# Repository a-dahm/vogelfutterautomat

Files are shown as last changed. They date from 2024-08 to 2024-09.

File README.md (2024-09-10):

<p align="center">
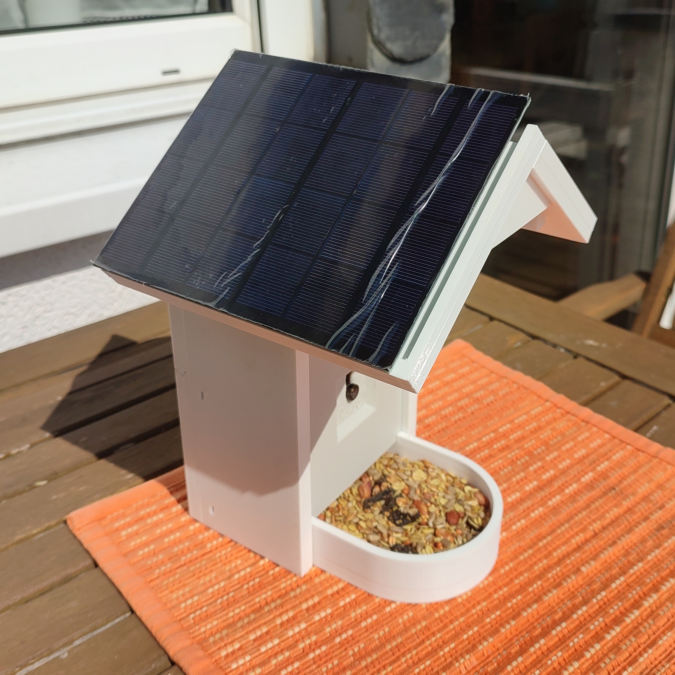
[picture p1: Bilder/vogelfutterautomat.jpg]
    
</p>

`⚠️ Dieses Projekt befindet sich zurzeit noch in der Prototyp-Phase. Der Prototyp ist funktionstüchtig, jedoch gibt es noch viel zu verbessern, damit das Gerät tatsächlich einen einsetzbaren Zustand erreicht. ⚠️`

<!-- omit in toc -->
# Inhaltsverzeichnis

- [Vogelfutterautomat](#vogelfutterautomat)
  - [Funktionsweise](#funktionsweise)
  - [Repository-Übersicht](#repository-übersicht)
  - [Materialübersicht](#materialübersicht)
  - [Anleitung](#anleitung)
    - [Firmware](#firmware)
      - [Arduino Pro Mini 3V](#arduino-pro-mini-3v)
      - [Seeed Studio XIAO ESP32S3 Sense](#seeed-studio-xiao-esp32s3-sense)
    - [Server](#server)
    - [Elektronik](#elektronik)
    - [Gehäuse](#gehäuse)
      - [Merkmale](#merkmale)
      - [Zusammenbau](#zusammenbau)

# Vogelfutterautomat

Bei diesem Projekt handelt es sich um einen Vogelfutterautomat mit integrierter Kamera und Mikrofon zur automatischen Durchführung von Bild- und Audioaufnahmen von Vögeln. Das Gerät kann die gesammelten Daten per WLAN an ein externes System übertragen oder diese auf einer SD-Karte speichern.

## Funktionsweise

Das Gerät basiert auf der Kombination eines Arduino Pro Mini und einem Seeed Studio XIAO ESP32S3 Sense. Als Stromversorgung dient ein Li-Po-Akku in Kombination mit einer Solarzelle und dem Solar Power Manager Board von DFRobot.

Der ESP32S3 führt mithilfe eines OV2640 Kamera-Moduls und dem integrierten Mikrofon Aufnahmen durch. Um den Stromverbrauch zu verringern wird die Stromversorgung des ESP32S3 durch den Arduino Pro Mini gesteuert. Der Arduino Pro Mini befindet sich dabei die meiste Zeit im Stromsparenden Deep-Sleep-Modus und wird mithilfe eines DS3231 Real-Time-Clock-Moduls sowie einem M5Stack AS312 PIR Bewegungssensor aufgeweckt.

Die Elektronik ist also wie folgt aufgebaut:

<p align="center">
    
</p>

Je nach Firmware-Konfiguration werden bei jeder Aufweckung Foto- und Audio-Aufnahmen durch den ESP32S3 erhoben. Die Daten können dann entweder auf einer SD-Karte gespeichert oder per WLAN an einen dafür eingerichteten Webserver übertragen werden.

## Repository-Übersicht

* Arduino: Firmware für den Arduino Pro Mini 3V
* ESP: Firmware für den Seeed Studio XIAO ESP32S3 Sense
* Elektronik: Zeichnung des Schaltkreises.
* Bilder: Enthält die in diesem Dokument verwendeten Bilder
* Gehäuse: STL- und Sketchup-Dateien für den 3D-Druck des Gehäuses
* Server: Software für den PHP-Server

## Materialübersicht

Das gesamte für den Zusammenbau benötigte Material (mit beispielhaften Links wo angebracht):

* Arduino Pro Mini 3V ([Berrybase](https://www.berrybase.de/arduino-pro-mini-328-3.3v/8mhz))
* Seeed Studio XIAO ESP32S3 Sense ([Berrybase](https://www.berrybase.de/seeed-xiao-esp32s3-sense-esp32-s3r8-wlan-ble-5.0-ov2640-kamerasensor-8mb-psram-8mb-flash))
* DS3231 Real-Time-Clock-Modul ([Eckstein-Shop](https://eckstein-shop.de/DS3231RTCModulI2CAT24C32forArduino2CwithLIR2032BatteryEN))
* PIR Modul ([Robotshop](https://eu.robotshop.com/de/products/m5stack-pir-bewegungssensor-as312))
* DFRobot Solar Power Manager ([Eckstein-Shop](https://eckstein-shop.de/DFRobotSolarPowerManager5VEN))
* Li-Po Akku
* Solarzelle
* OV2640 mit langem Ribbon-Cable und Weitwinkellinse ([Amazon](https://amazon.de/dp/B0BXSL76L8))
* 6x M3-Schraube sowie Mutter für die Fixierung des Gehäuses
* 4x M2-Schraube sowie Mutter für die Befestigung der Platine im Gehäuse
* Lochraster-Platine (70 x 50 mm) ([Eckstein-Shop](https://eckstein-shop.de/Lochrasterplatine50x70mmExperimentierplatineLC3B6tplatinePrototypeLeiterplattePCB2StC3BCcke))
* Lötmaterial (Platine, Verbindungskabel, Stiftleisten)

## Anleitung

### Firmware

Für das Anpassen und Überspielen der Firmware auf die beiden Mikroprozessor-Boards wird die [Arduino IDE](https://www.arduino.cc/en/software) benötigt. Als Einführung hier die offizielle (englische) Anleitung: [Link](https://docs.arduino.cc/software/ide-v2/tutorials/getting-started-ide-v2/)

Es werden für die Kompilierung die folgenden Bibliotheken benötigt, die zuvor über die Arduino IDE installiert werden müssen:

* [Low-Power (Rocket Scream Electronics)](https://www.arduino.cc/reference/en/libraries/low-power/): Verwaltung des Deep-Sleep-Modus für den Arduino Pro Mini 3V
* [RTCLib (Adafruit)](https://www.arduino.cc/reference/en/libraries/rtclib/): Kommunikation mit dem DS3231 Real-Time-Clock-Modul via I2C auf dem ESP32S3
* [NTPClient (Fabrice Weinberg)](https://www.arduino.cc/reference/en/libraries/ntpclient/): Für die Ermittlung der Uhrzeit via WLAN für das DS3231 Real-Time-Clock-Modul

#### Arduino Pro Mini 3V

Die Firmware für den Arduino Pro Mini befindet sich unter `Arduino/Arduino.ino`. Es sind hier keine Anpassungen am Quellcode notwendig.

Es ist jedoch wichtig zu beachten, dass vor dem Überspielen in der Arduino IDE unter "Werkzeuge" > "Processor" der Wert "ATmega328P (3,3V, 8 MHz)" ausgewählt wird (anstelle der 5V Variante):

<p align="center">
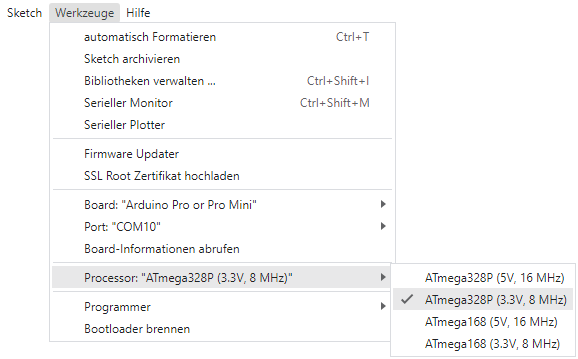
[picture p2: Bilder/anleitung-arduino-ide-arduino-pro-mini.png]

</p>

#### Seeed Studio XIAO ESP32S3 Sense

Die Firmware für den Seeed Studio XIAO ESP32S3 Sense befindet sich unter `ESP/ESP.ino`. Im Quellcode können die folgenden Einstellungen vorgenommen werden:

| Einstellung | Beschreibung | Beispiel |
| --- | --- | --- |
| `SERIAL_DEBUG` | Kann für Debug-Zwecke definiert werden, um Informationen über die UART-Schnittstelle des ESP32S3 ausgeben zu lassen | `//#define SERIAL_DEBUG` (deaktiviert) |
| `DATEN_MODUS` | Bestimmt, wie die mit den gesammelten Daten umgegangen wird. `DIREKT_UPLOAD`: Daten werden sofort bei Aufnahme hochgeladen und nicht zwischengespeichert. In diesem Modus wird keine SD-Karte benötigt. `TAEGLICHER_UPLOAD`: Aufnahmen werden auf der SD-Karte zwischengespeichert und am nächsten Morgen hochgeladen. `LOKAL`: Aufnahmen werden nur auf der SD-Karte gespeichert; die WLAN-Funktion wird hierbei dennoch eventuell für die Ermittlung der Uhrzeit verwendet, falls das RTC-Modul ausfällt. | `#define DATEN_MODUS DIREKT_UPLOAD` |
| `WARTE_VOR_FOTO` | Gibt eine Zeit (in Sekunden) an, die zwischen hochfahren und Foto gewartet werden soll. Dies dient dazu, dass sich der Kamera-Sensor an die Helligkeit der Umgebung anpassen kann, um unter-/überbelichteten Fotos vorzubeugen. | `#define WARTE_VOR_FOTO 2` |
| `AUDIOAUFNAHME_KURZ_DAUER` | Bestimmt die Länge der Audioaufnahme (in Sekunden) bei Aufweckung durch den Bewegungssensor. Maximalwert: 240 Sekunden. | `#define AUDIOAUFNAHME_KURZ_DAUER 5` |
| `AUDIOAUFNAHME_LANG_DAUER` | Bestimmt die Länge der Audioaufnahme (in Sekunden) bei Aufweckung durch das Real-Time-Clock-Modul. Dies dient dazu, den Vogelgesang am Morgen festzuhalten. Maximalwert: 240 Sekunden. | `#define AUDIOAUFNAHME_LANG_DAUER 60` |
| `WIFI_SSID` | Der Name des WLAN-Netzwerkes. | `#define WIFI_SSID "MeinWLAN"` |
| `WIFI_PASSWORD` | Das Passwort des WLAN-Netzwerkes. | `#define WIFI_PASSWORD "MeinPasswort"` |
| `UPLOAD_SERVER` | Die IP-Adresse des Webservers. | `#define UPLOAD_SERVER "192.168.178.50"` |
| `UPLOAD_PORT` | Der vom Webserver verwendete Port. Normalerweise ist dies bei HTTP der Port 80. | `#define UPLOAD_PORT 80` |
| `UPLOAD_PATH` | Der Pfad zum `upload.php`-Skript auf dem Webserver. Bei Ablage im Root-Verzeichnis lautet dieser `/upload.php` | `#define UPLOAD_PATH "/upload.php"` |

Vor dem Überspielen der Firmware muss unter "Werkzeuge" > "PSRAM" der Wert "OPI PSRAM" ausgewählt werden:

<p align="center">
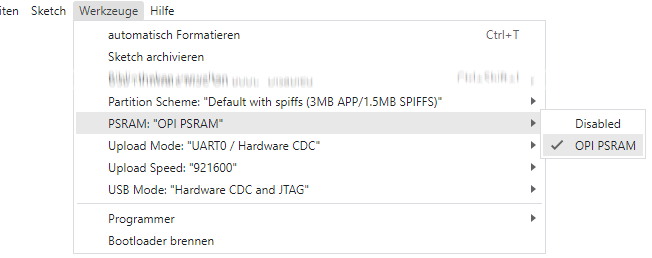
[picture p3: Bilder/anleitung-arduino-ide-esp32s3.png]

</p>

### Server

Die Server-Seite verwendet HTML & PHP. Dafür muss eine entsprechende Server-Software auf einem geeigneten Gerät installiert werden. Das verwendete Gerät sollte soweit möglich durchgehend erreichbar sein, damit jederzeit Uploads stattfinden können. Es wird daher empfohlen, dafür zum Beispiel einen Raspberry Pi oder einen Mini-PC zu verwenden.

Um die Server-Seite zu hosten wird Apache & PHP verwendet. Die Installation dieser Komponenten hängt vom Betriebssystem ab:

* Unter Windows kann [XAMPP](https://www.apachefriends.org/de/index.html) verwendet werden.
* Für eine Anleitung zur Installation von Apache & PHP unter Linux sollte je nach Distribution nach einer Anleitung gesucht werden. Beispielsweise hier die [Installation unter Ubuntu](https://wiki.ubuntuusers.de/PHP/#Installation-fuer-serverseitige-Programmierung).

Nach der Installation können die Dateien aus dem "Server"-Verzeichnis dieses Repositories im entsprechenden Root-Verzeichnis des Webservers abgelegt werden: unter Windows der Ordner `Apache\htdocs`, unter Linux standardmäßig `/var/www/html`. Falls die Dateien in einem Unterverzeichnis abgelegt werden (zum Beispiel weil bereits andere Webseiten gehostet werden) muss der entsprechende Pfad in der `ESP.ino` eingetragen werden.

In dem Verzeichnis befinden sich auch zwei Log-Dateien `log.txt` und `errors.txt`. In diese Textdateien werden nach jedem erfolgten Upload rudimentäre Informationen festgehalten um potentielle Probleme zu diagnostizieren.

Damit die Webseite durch den ESP32S3 gefunden werden kann muss die IP-Adresse in der `ESP.ino` eingetragen werden (unter `#define UPLOAD_SERVER`).

* Anleitung für Windows [hier](https://support.microsoft.com/de-de/windows/suchen-sie-ihre-ip-adresse-in-windows-f21a9bbc-c582-55cd-35e0-73431160a1b9)
* Anleitung für Linux [hier](https://www.ionos.de/digitalguide/hosting/hosting-technik/linux-ip-adresse-anzeigen/)

### Elektronik

Der Schaltplan der Platine ist im Verzeichnis `Elektronik` zu finden. Die `.fzz`-Datei kann mit der Software [Fritzing](https://fritzing.org/) eingesehen werden. Bei Fritzing handelt es sich zwar um Open-Source Software, jedoch wird die kompilierte Version nur gegen Zahlung vertrieben. Falls die Software also nicht verwendet werden kann, finden Sie hier einen Screenshot des Schaltplans:

<p align="center">
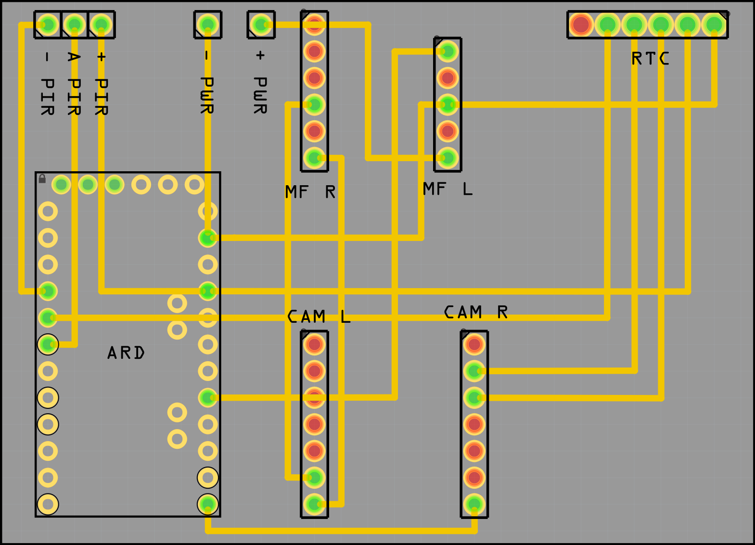
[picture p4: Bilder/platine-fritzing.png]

</p>

Dabei wurden für die Anschlüsse mit der Bezeichnung `-/A/+ PIR` (oben links) einfache Stiftleisten verwendet. Für `-/+ PWR` (oben links) wurden Schraubklemmen gewählt. Das RTC-Modul (rechts) wurde mit 90° gebogenen Stiften versehen und deshalb auch mit 90°-Winkel Stiftleisten auf der Platine befestigt.

Die fertiggestellte Platine inklusive der einzelnen Komponenten sieht Schlußendlich wie folgt aus:

<p align="center">
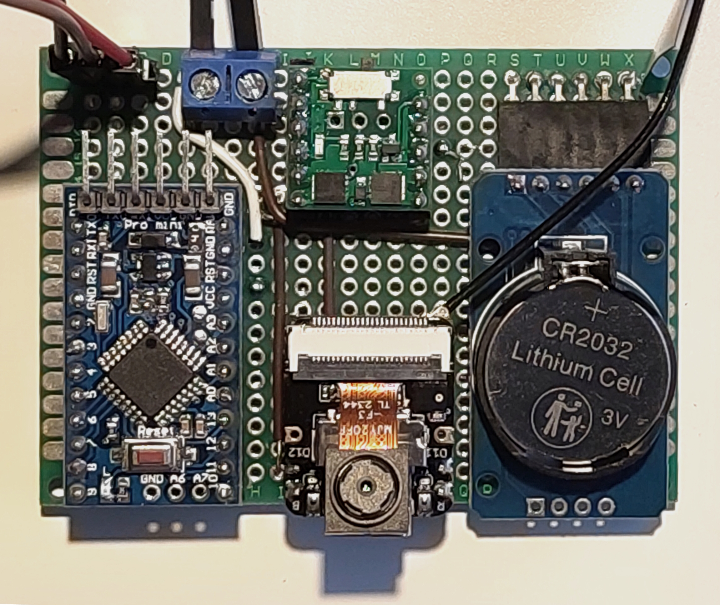
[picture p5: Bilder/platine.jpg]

</p>

### Gehäuse

Die Modell-Dateien für das Gehäuse können im Verzeichnis `Gehäuse` gefunden werden.

Das Gehäuse wurde für die Herstellung mittels 3D-Druck konzipiert. Neben den einzelnen Bauteilen im `STL`-Dateiformat wurde auch das komplette Modell als [Sketchup](https://www.sketchup.com/)-Datei (`SKP`-Dateiformat) hinterlegt. Dadurch können eigene Anpassungen durchgeführt werden, soweit dies erforderlich ist.

<p align="center">
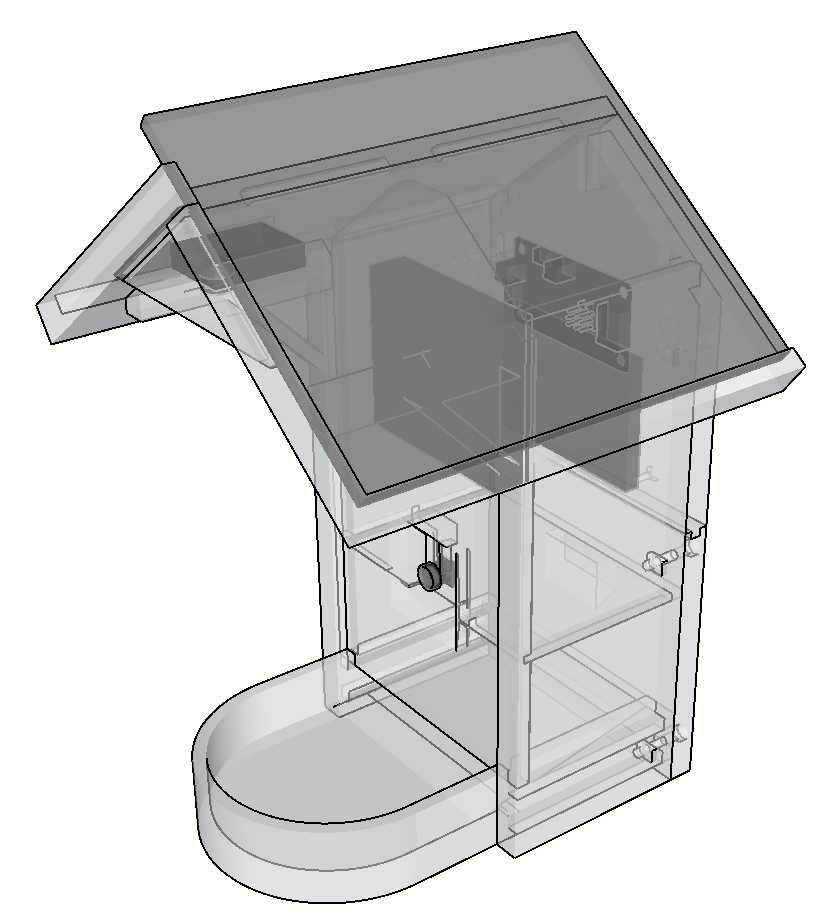
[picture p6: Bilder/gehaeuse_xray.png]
    
</p>

In der Sketchup-Datei wurden auch die restlichen Komponenten, wie beispielsweise die Solarzelle und das Kamera-Modul, eingezeichnet. Falls sich diese Maße von denen Ihrer Komponenten unterscheided, was beispielsweise bei der gelöteten Platine der Fall sein kann, müssen eventuell hier Anpassungen durchgeführt werden.

Falls kein eigener 3D-Drucker zur Verfügung steht kann die Produktion des Gehäuses auch durch einen Dienstleister durchgeführt werden lassen. Dazu reicht es aus, die `STL`-Dateien an diesen zu übergeben.

Bei der eigenen Herstellung sollte darauf geachtet werden, ob es möglich ist, ein Hitzebeständigeres Material als PLA zu verwenden, da dieses eventuell unter intensiver Sonneneinstrahlung die Erweichungstemperatur erreicht. Empfohlen wird hier der Druck mittels PETG-Filament. Die Druckzeit unterscheided sich je nach Drucker, Filament und Konfiguration immens. Ein Testdruck, der auf einem Prusa I3 MK3S+ mit PETG-Filament durchgeführt wurde, dauerte insgesamt circa 45 Stunden.

Fast alle Bauteile des Gehäuses werden per Steckverbindung zusammengefügt. Dabei kann die Toleranz dieser Verbindungen jedoch nicht im Allgemeinen für jeden Drucker korrekt in den gebotenen Modell-Dateien geboten werden. Daher wird es sehr wahrscheinlich notwendig sein, die einzelnen Steckverbindungen mit Feile oder anderen Schleifmethoden nachzubearbeiten, bis die Steckverbindungen der Bauteile zusammenpassen.

#### Merkmale

Die Solarzelle kann beliebig links oder rechts auf dem Dach platziert werden. Das Verbindungskabel wird dann über die Rückseite durch eine Öffnung direkt unterhalb des Daches in die innere Kammer geführt:

<p align="center">
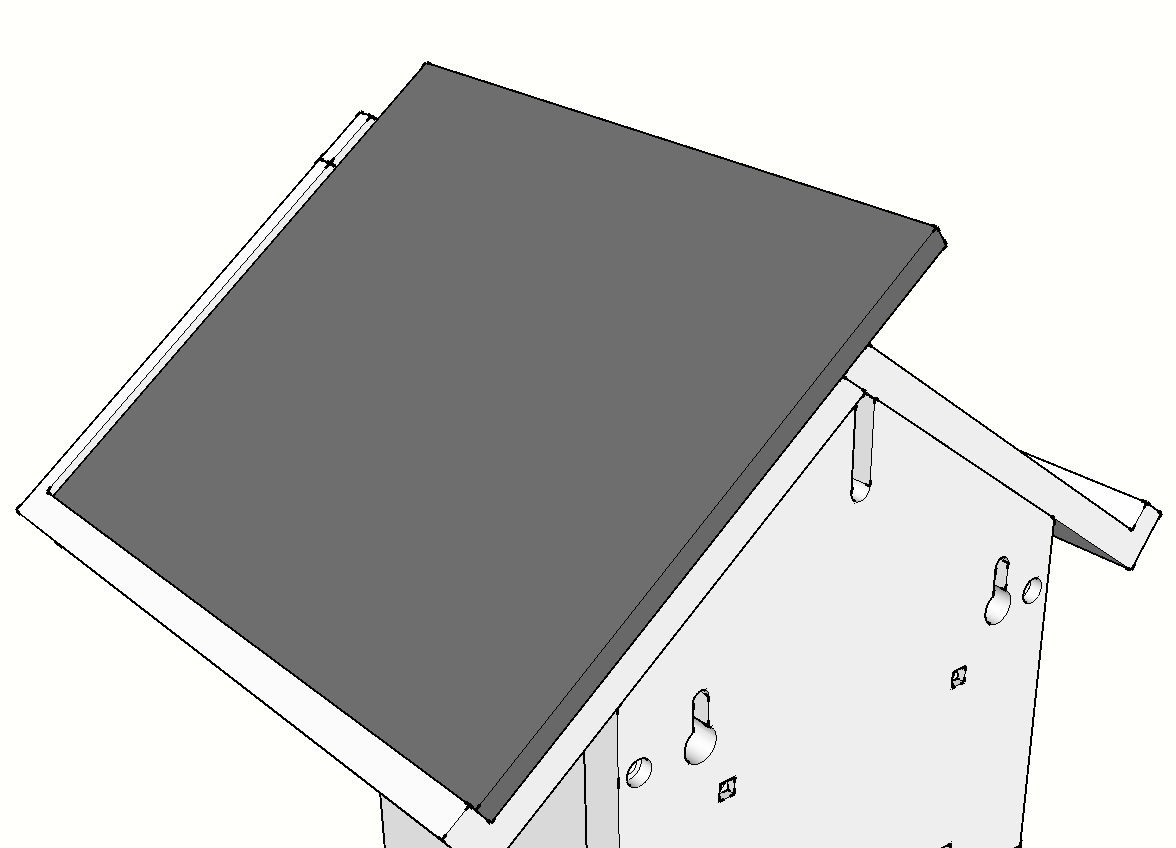
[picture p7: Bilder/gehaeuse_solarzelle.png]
    
</p>

Der PIR-Bewegungssensor wurde unter dem Dach platziert und nach unten auf den Futtertrog ausgerichtet. Die Kabel des Sensors werden unter dem Dach durch eine Öffnung ins Innere geführt:

<p align="center">
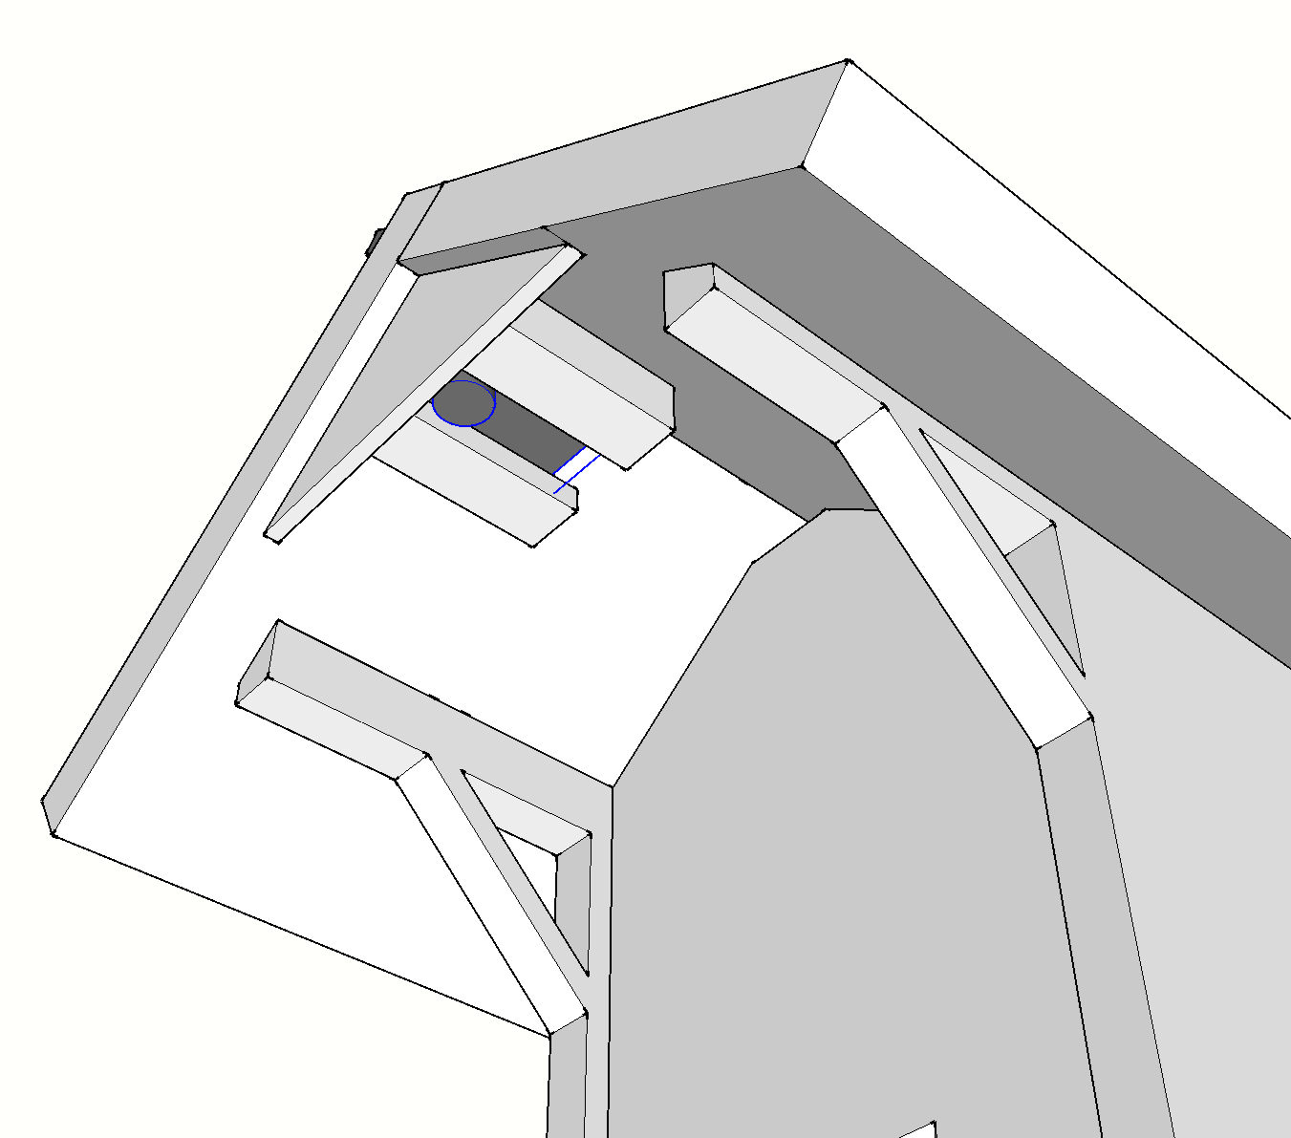
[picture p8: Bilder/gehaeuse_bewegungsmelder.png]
    
</p>

Die Linse des OV2640-Kamera-Moduls wird auf der Vorderseite des Gehäuse platziert. Diese wird von oben in einen Schlitz eingeführt, um die Linse zu fixieren:

<p align="center">
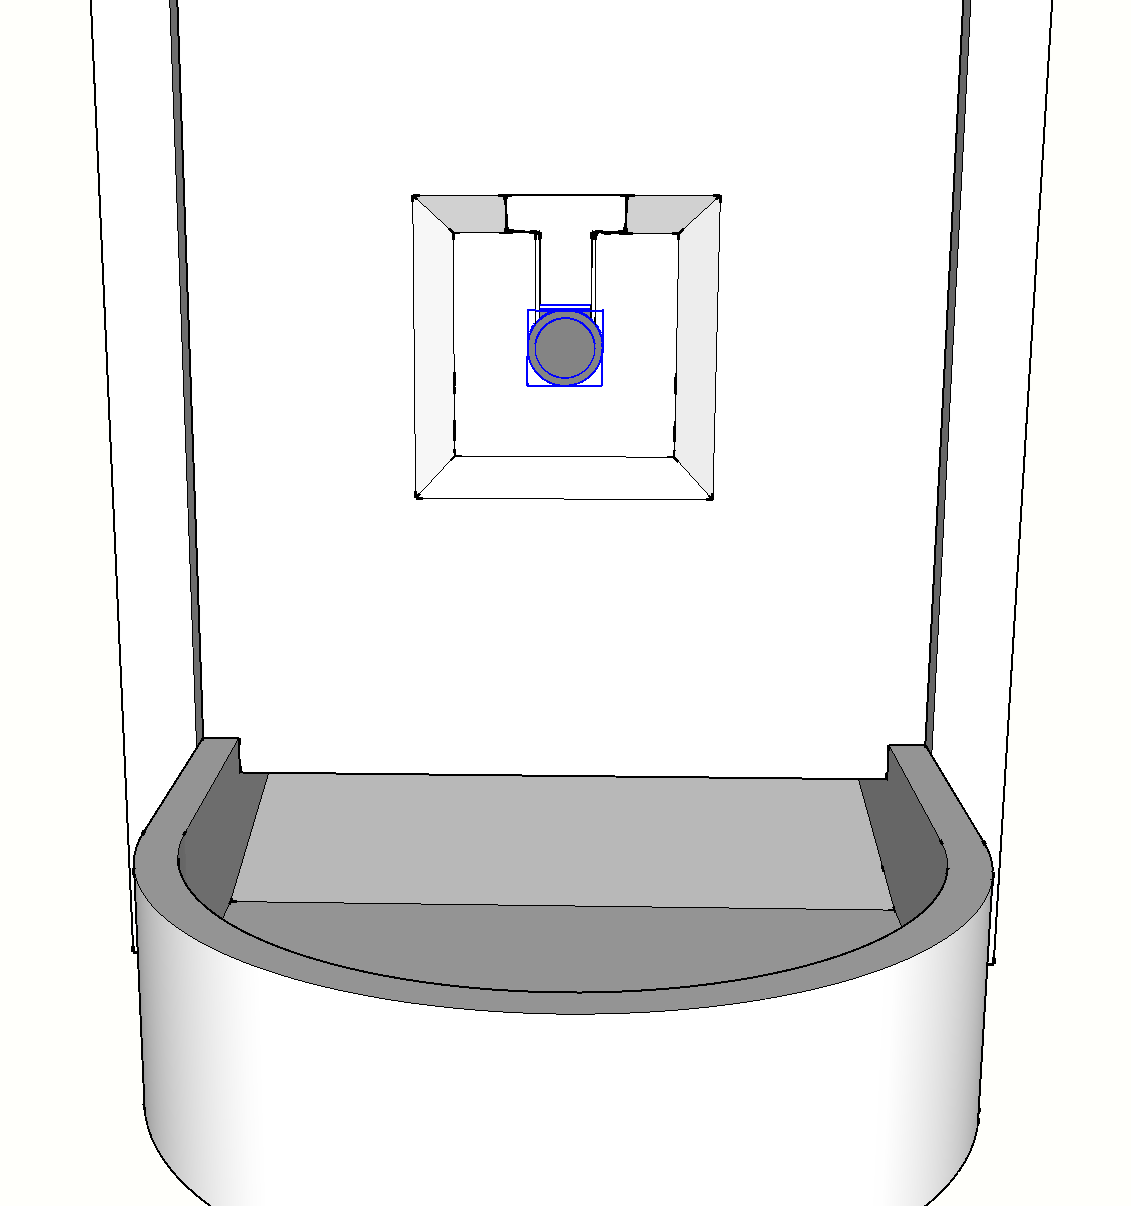
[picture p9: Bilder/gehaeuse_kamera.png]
    
</p>

Die restliche Elektronik wurde im inneren des Gehäuses platziert. Der Li-Po Akku (links) wird mit doppelseitigem Klebeband über der Kamera an der Vorderwand fixiert. Das DFRobot Solar Power Manager Board wird ohne fixierung im unteren Bereich abgelegt. Die Platine mit den restlichen Komponenten (rechts) wird gegenüber der Kamera mittels 4 M2 Schrauben und Muttern an der Rückwand befestigt.

<p align="center">
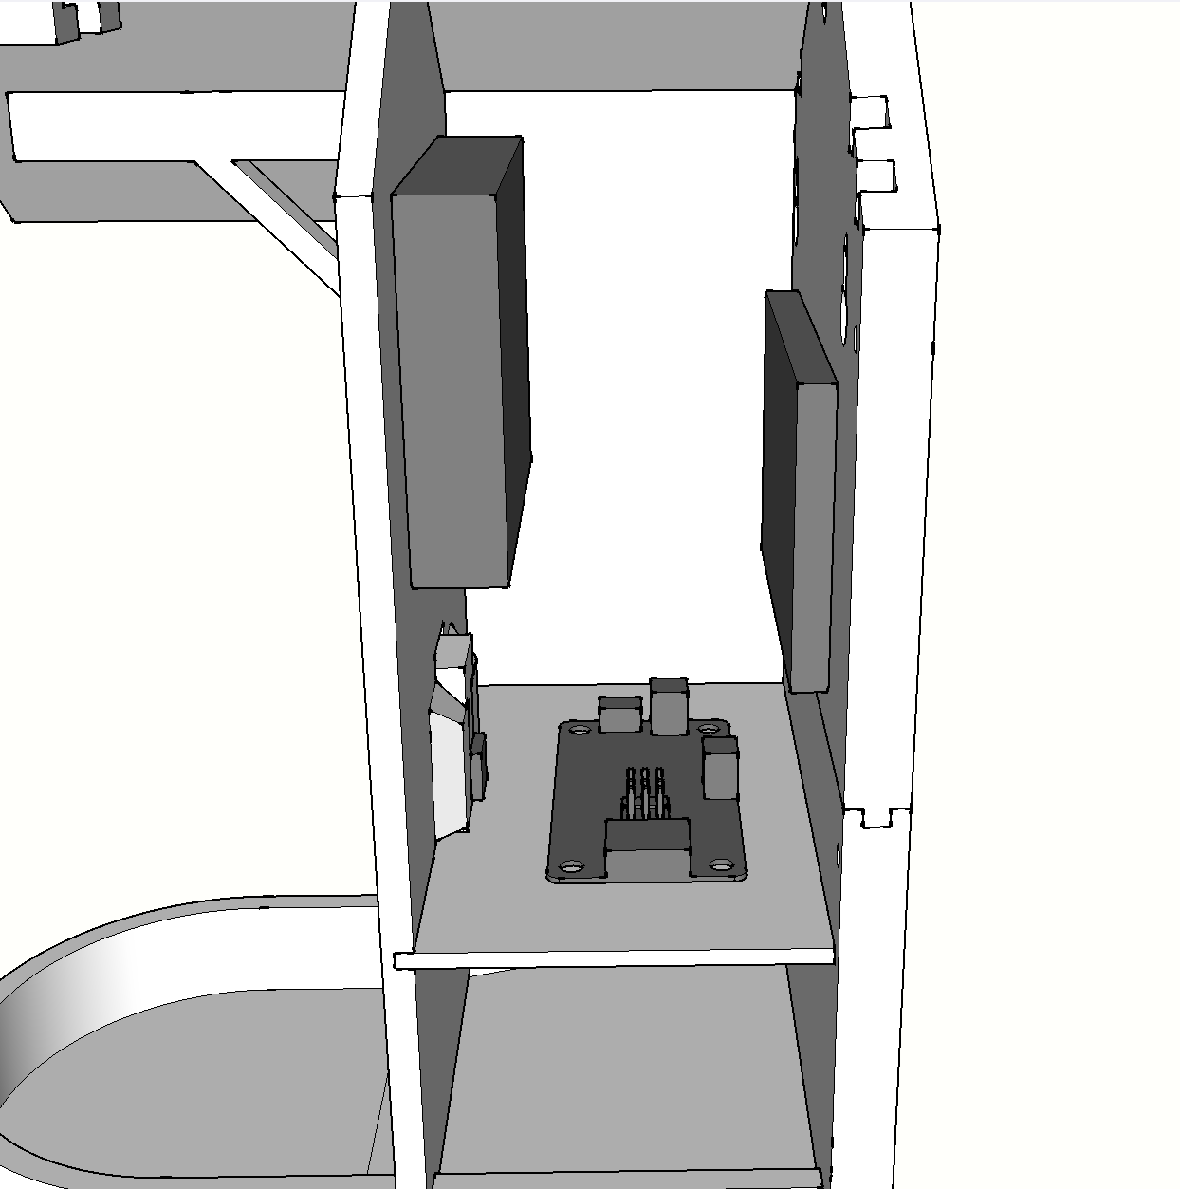
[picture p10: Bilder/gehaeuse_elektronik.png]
    
</p>

Auf der Rückseite des Gehäuse befindet sich eine Öffnung, um Vogelfutter nachzufüllen. Zudem befinden sich hier zwei Öffnungen, durch die der Vogelfutterautomat mittels Schrauben an einer Hauswand befestigt werden.

<p align="center">
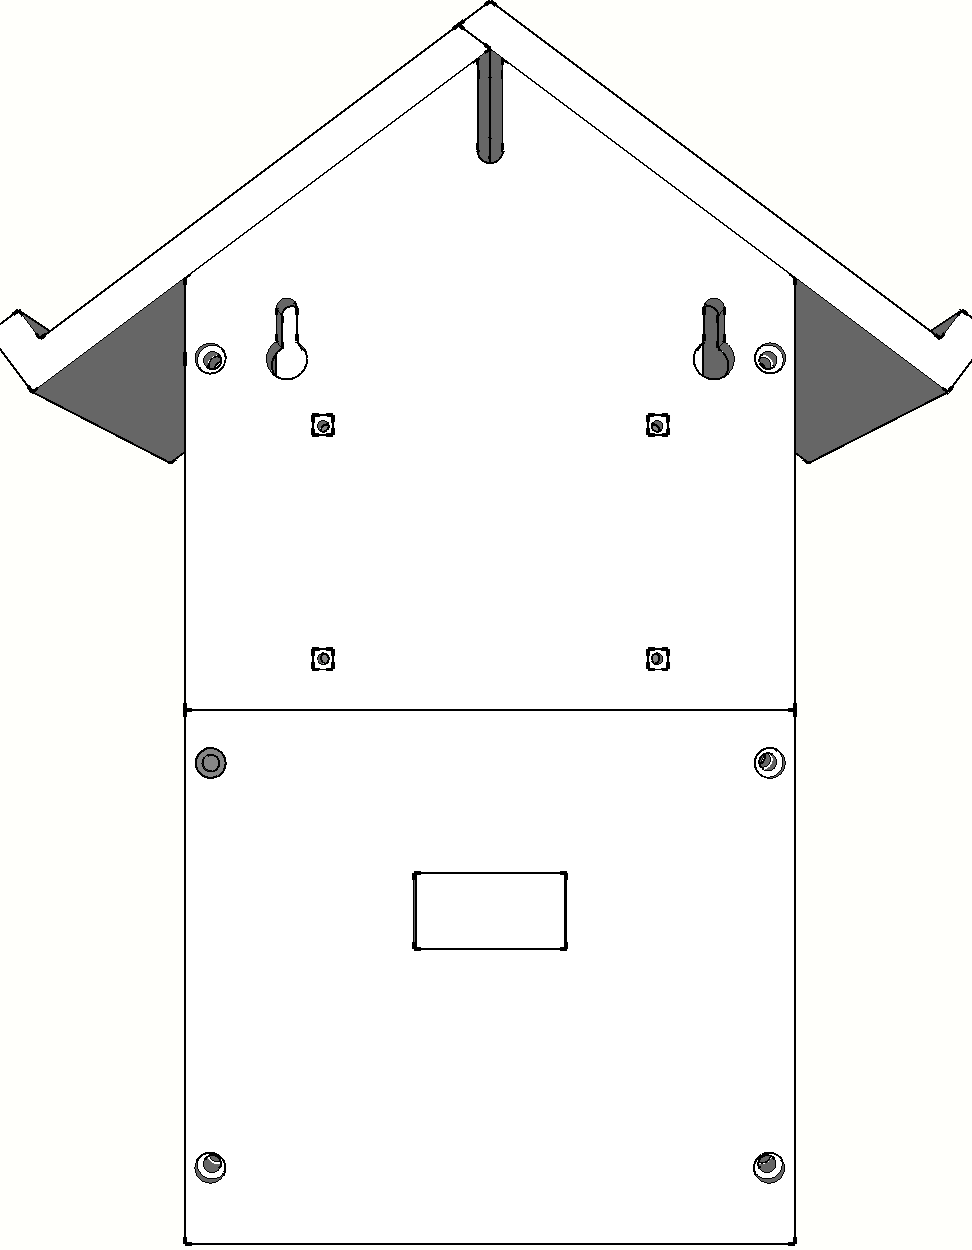
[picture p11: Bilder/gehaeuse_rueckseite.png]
    
</p>

#### Zusammenbau

Der Zusammenbau des Gehäuses ist weitestgehend selbsterklärend. Zunächst wird der Li-Po Akku mit doppelseitigem Klebeband an der Rückseite der Vorderwand befestigt. Dabei sollte darauf geachtet werden, dass das Kabel des Akkus nach unten ausgerichtet ist.

<p align="center">
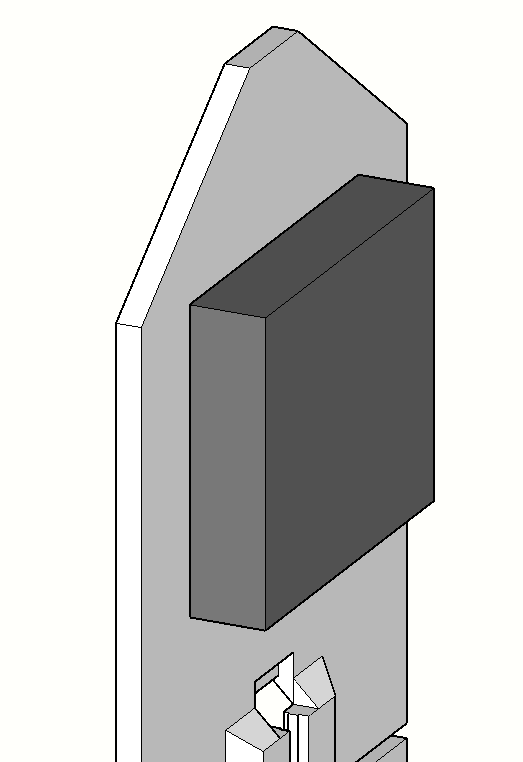
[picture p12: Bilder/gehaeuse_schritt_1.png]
    
</p>

Vom Futtertrog ausgehend werden die Vorderwand, der untere Teil der Rückwand und der Kammer-Separator zusammengesteckt:

<p align="center">
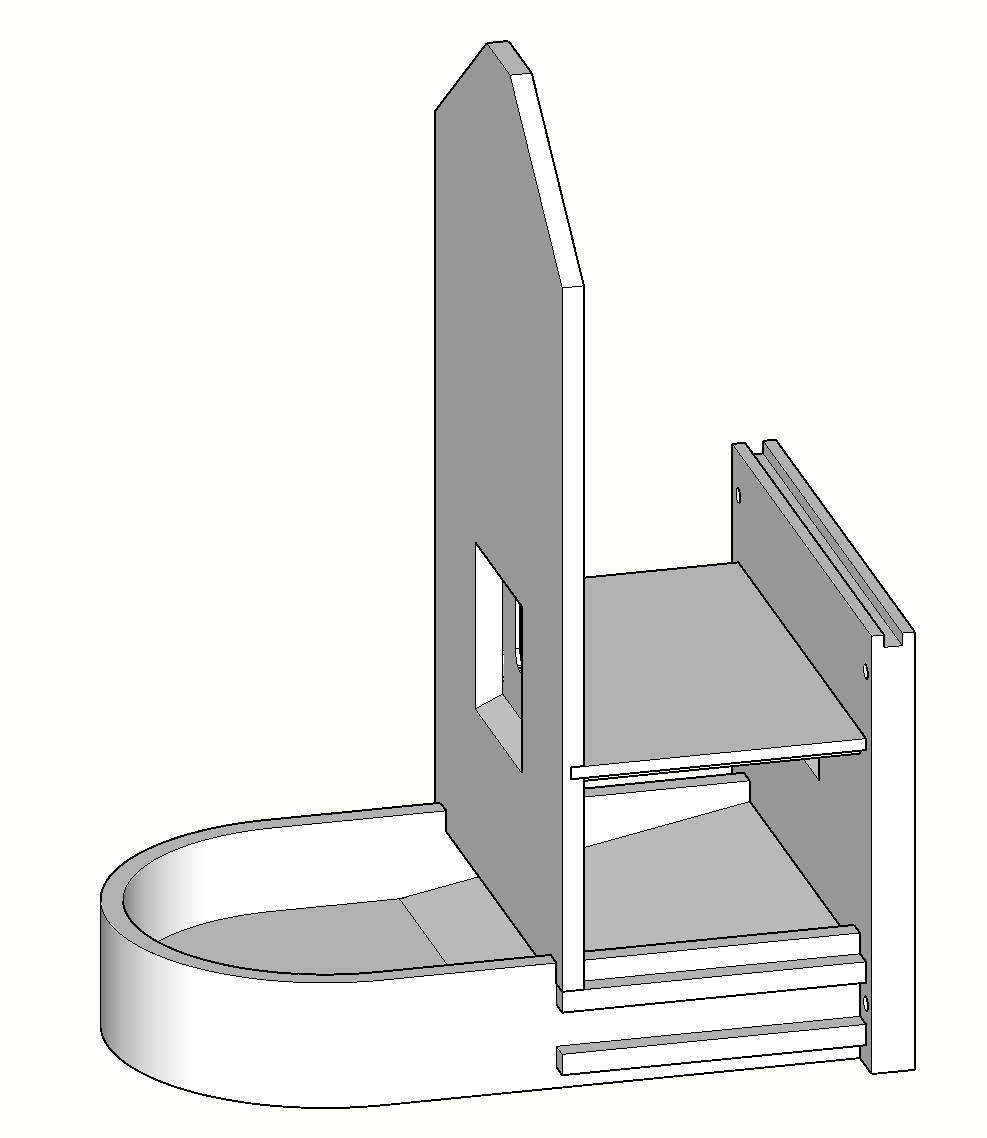
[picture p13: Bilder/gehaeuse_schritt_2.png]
    
</p>

Das Dach wird dann zunächst separat inklusive der PIR-Sensorhalterung zusammengesteckt:

<p align="center">
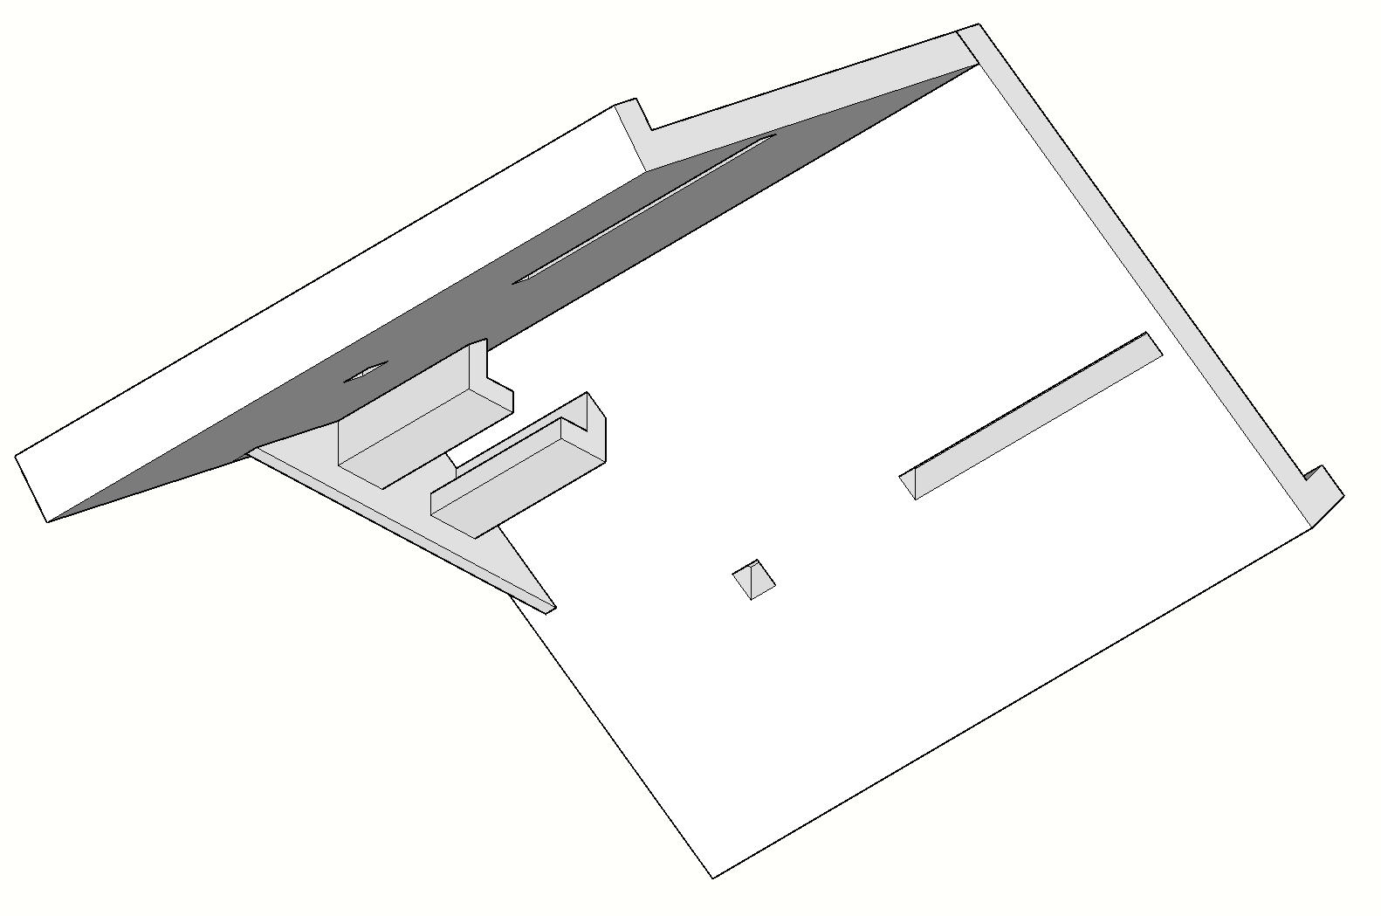
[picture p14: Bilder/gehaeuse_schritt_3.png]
    
</p>

Die Elektronik wird an der noch separierten oberen Rückwand mittels 4 M2 Schrauben und Muttern befestigt:

<p align="center">
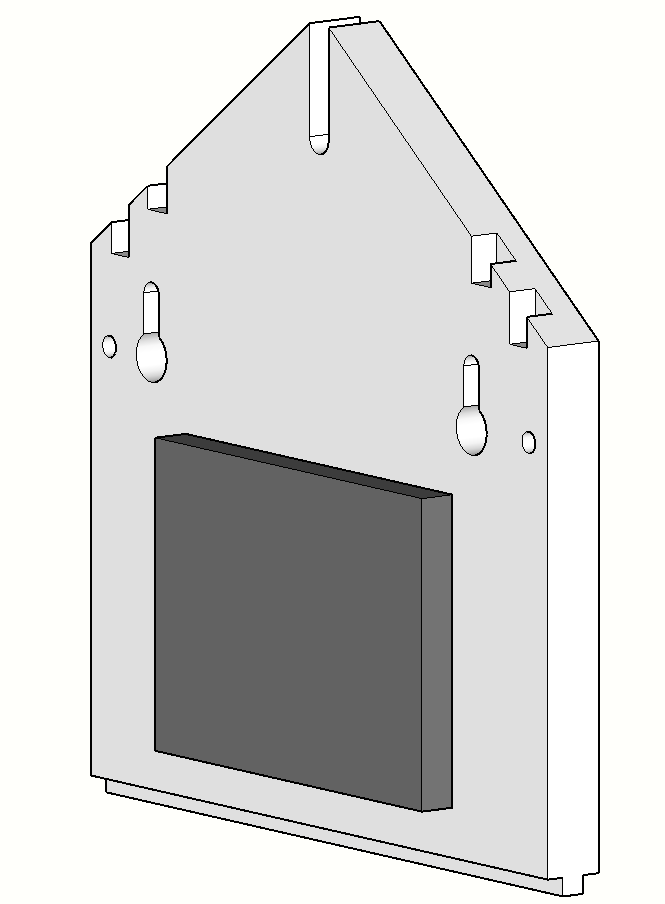
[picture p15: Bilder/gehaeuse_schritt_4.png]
    
</p>

Das Kamera-Modul wird dann von oben in die dafür vorgesehene Halterung in der Vorderwand eingeführt. Eventuell muss hierfür die Linse etwas verstellt werden:

<p align="center">
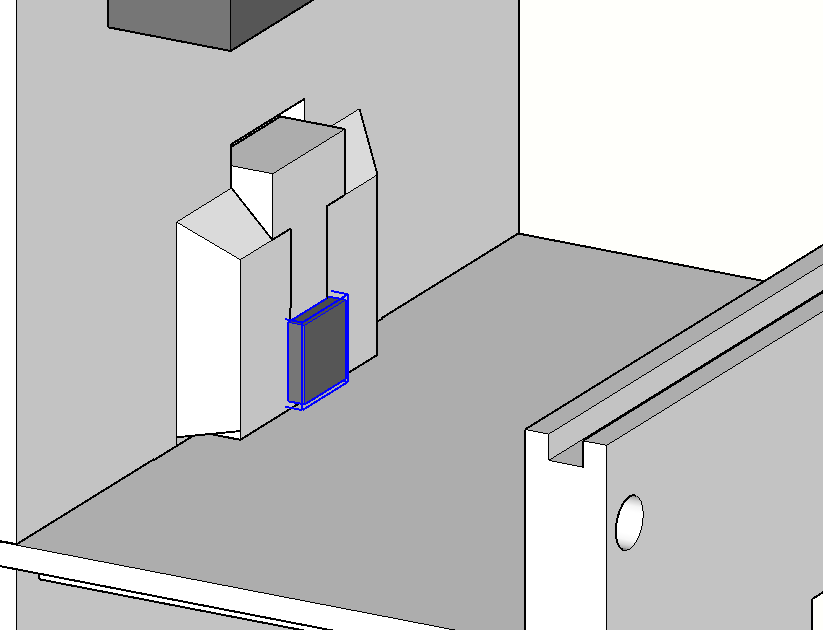
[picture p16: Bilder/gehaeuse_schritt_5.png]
    
</p>

Das Solar Power Manager Board wird dann im Inneren der Kammer platziert und zunächst nur mit dem Li-Po Akku verbunden:

<p align="center">
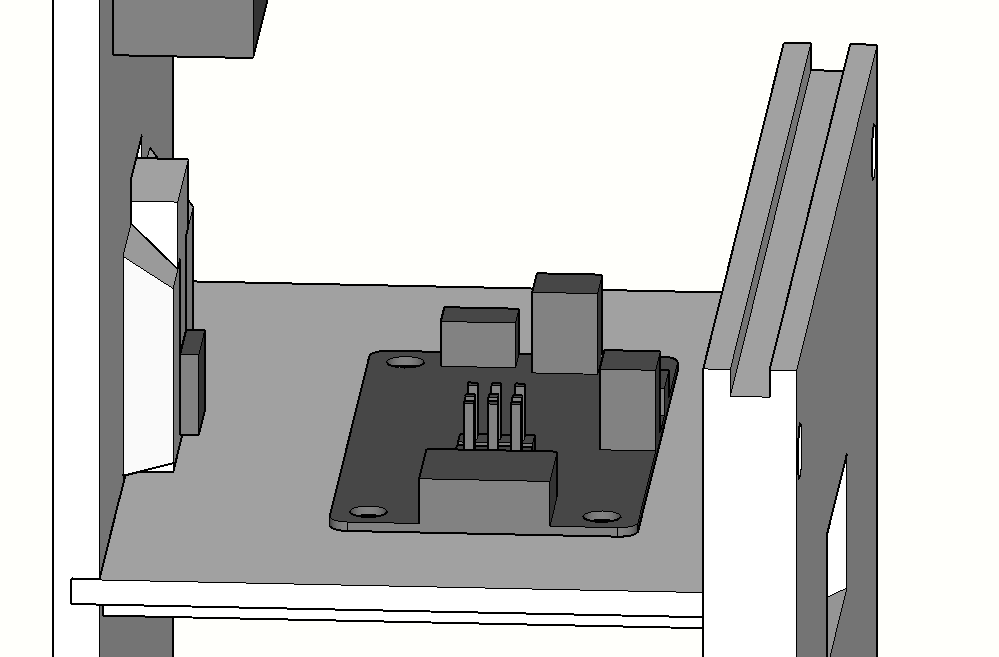
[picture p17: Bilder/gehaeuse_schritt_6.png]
    
</p>

Nun wird der obere Teil der Rückwand inklusive der Platine sowie eine der Seitenwände angesteckt. Die Seitenwand wird dann mit 3 M3 Schrauben und Muttern an den beiden Teilen der Rückwand fixiert. Dazu wird zunächst jeweils eine M3 Mutter in die dafür vorgesehenen rechteckigen Öffnungen auf den Seitenwänden gepresst, sodass diese nicht mehr rotieren kann. Dann kann durch die Rückwand hindurch jeweils eine M3 Schraube in jede Mutter eingeführt und fixiert werden:

<p align="center">
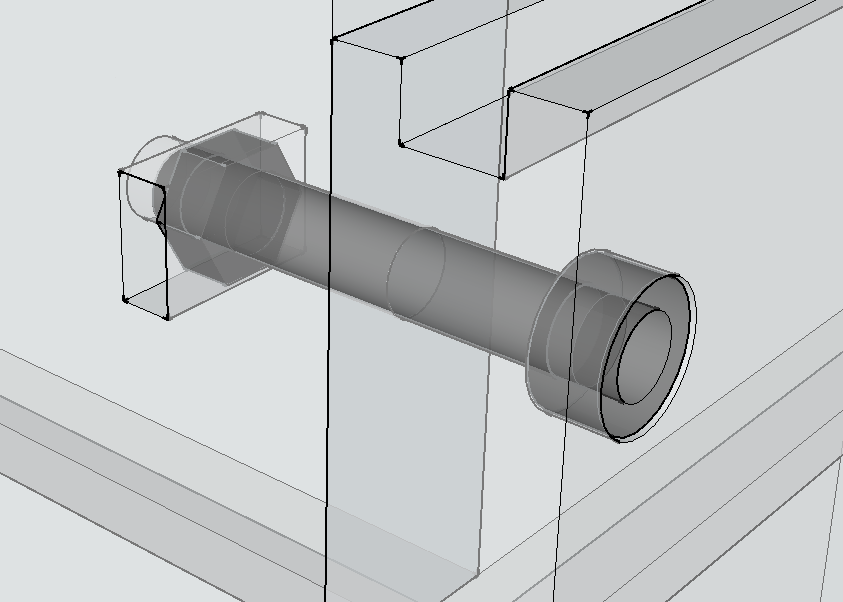
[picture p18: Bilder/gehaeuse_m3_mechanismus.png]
    
</p>

Nun kann die Stromversorgung des Solar Power Manager Boards mit der Platine verbunden werden. Zudem wird auch das Kamera-Modul an den XIAO ESP32S3 Sense angeschlossen.

<p align="center">
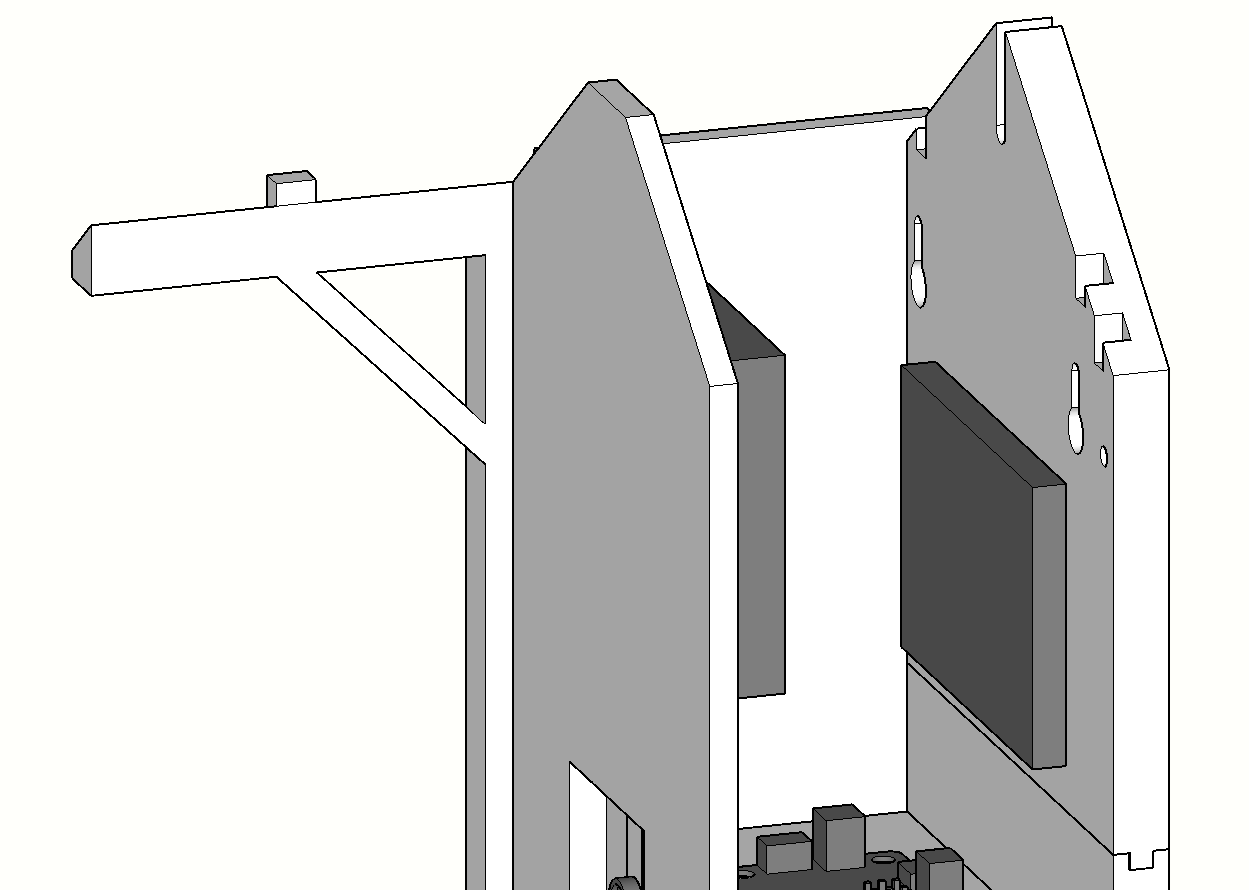
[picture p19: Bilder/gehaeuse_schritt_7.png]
    
</p>

Ohne das Dach bereits aufzustecken wird nun der Anschluss der Solarzelle durch die obere Öffnung der Rückwand geführt und an das Solar Power Manager Board angeschlossen. Zudem wird die Verkabelung des PIR-Bewegungsmelders mit der Platine durchgeführt. Falls dies in der Konfiguration der Firmware vorgesehen ist, wird in diesem Schritt auch die SD-Karte in den SD-Kartenleser des XIAO ESP32S3 Sense gesteckt. Jetzt kann die zweite Seitenwand angebracht werden. Diese wird ebenfalls durch 3 M3 Schrauben und Muttern an der Rückwand befestigt.

<p align="center">
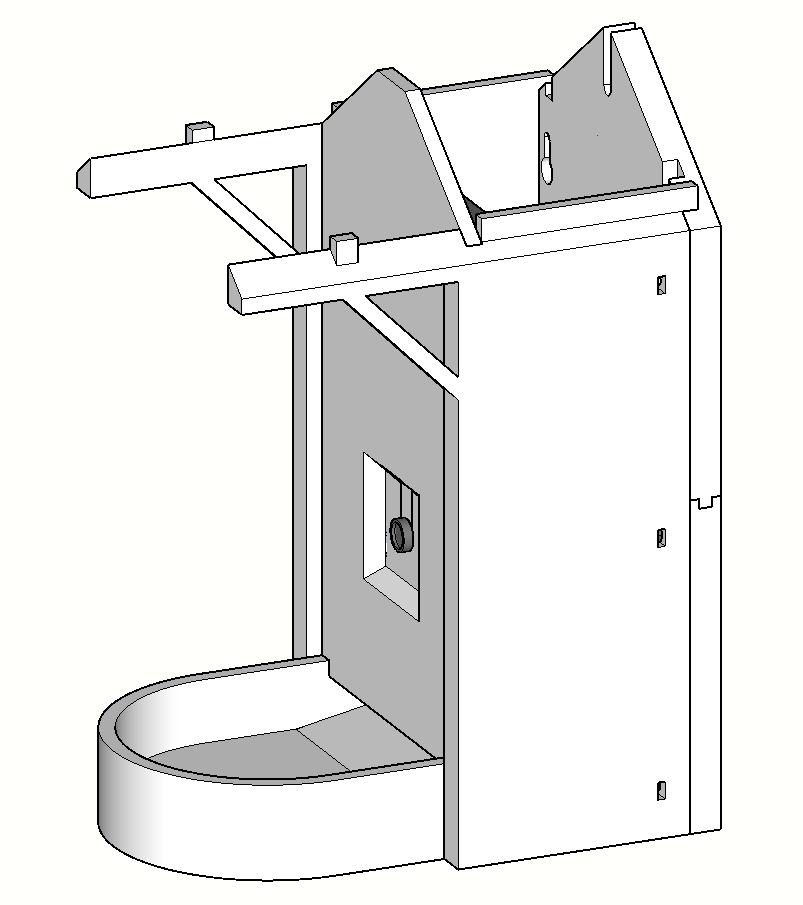
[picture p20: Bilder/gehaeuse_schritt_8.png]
    
</p>

Im letzten Schritt wird das Dach auf der Oberseite des Gerätes aufgesteckt. Hierbei muss darauf geachtet werden, dass die Kabel des PIR-Bewegungsmelder über die Flache Kante der Vorderwand von Außen in die innere Kammer geführt wurden, ohne dass diese durch das Dach gequetscht werden.

<p align="center">
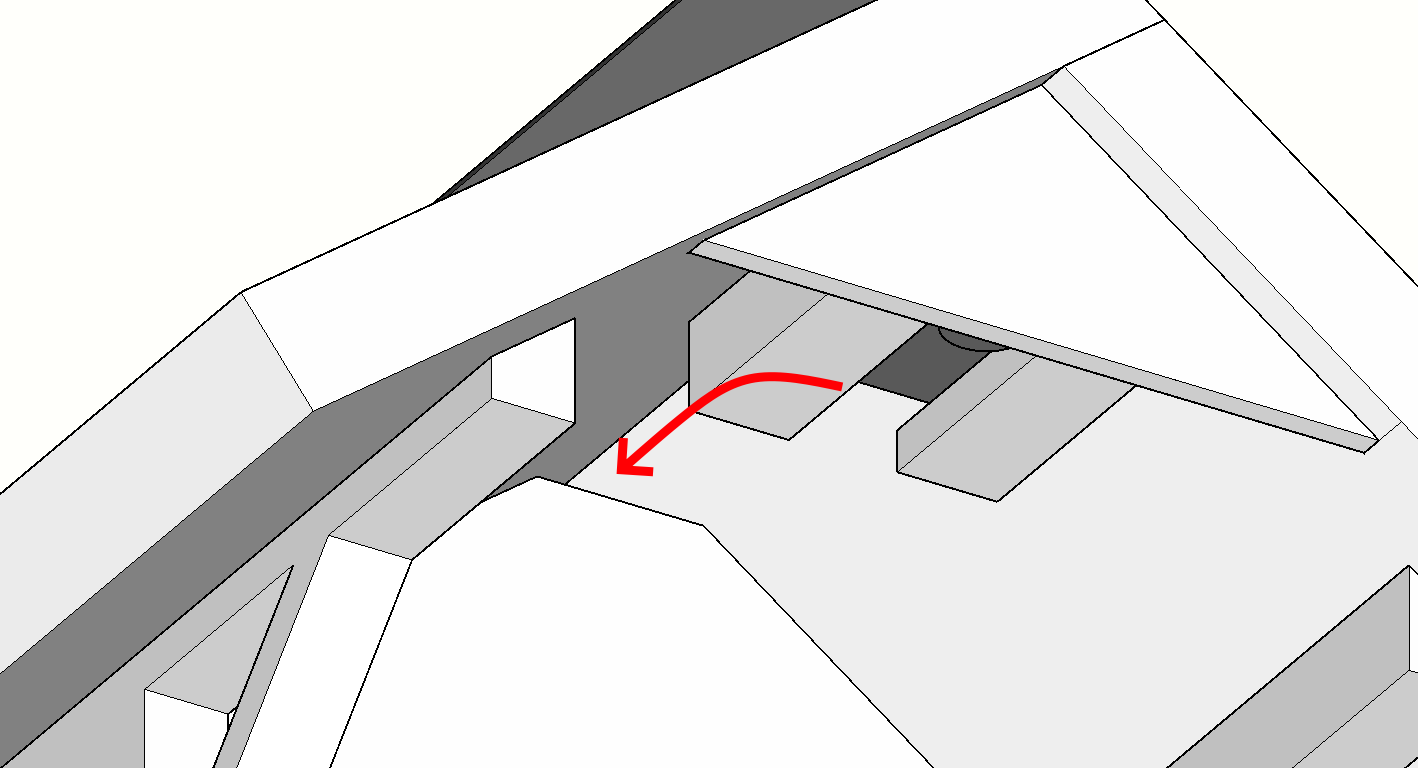
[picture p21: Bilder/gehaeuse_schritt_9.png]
    
</p>

Der PIR-Bewegungssensor wird dann in der dafür vorgesehenen Halterung an der Unterseite des Daches befestigt. Die Solarzelle wird auf der Seite des Daches platziert. Damit ist der Zusammenbau abgeschlossen.

<p align="center">
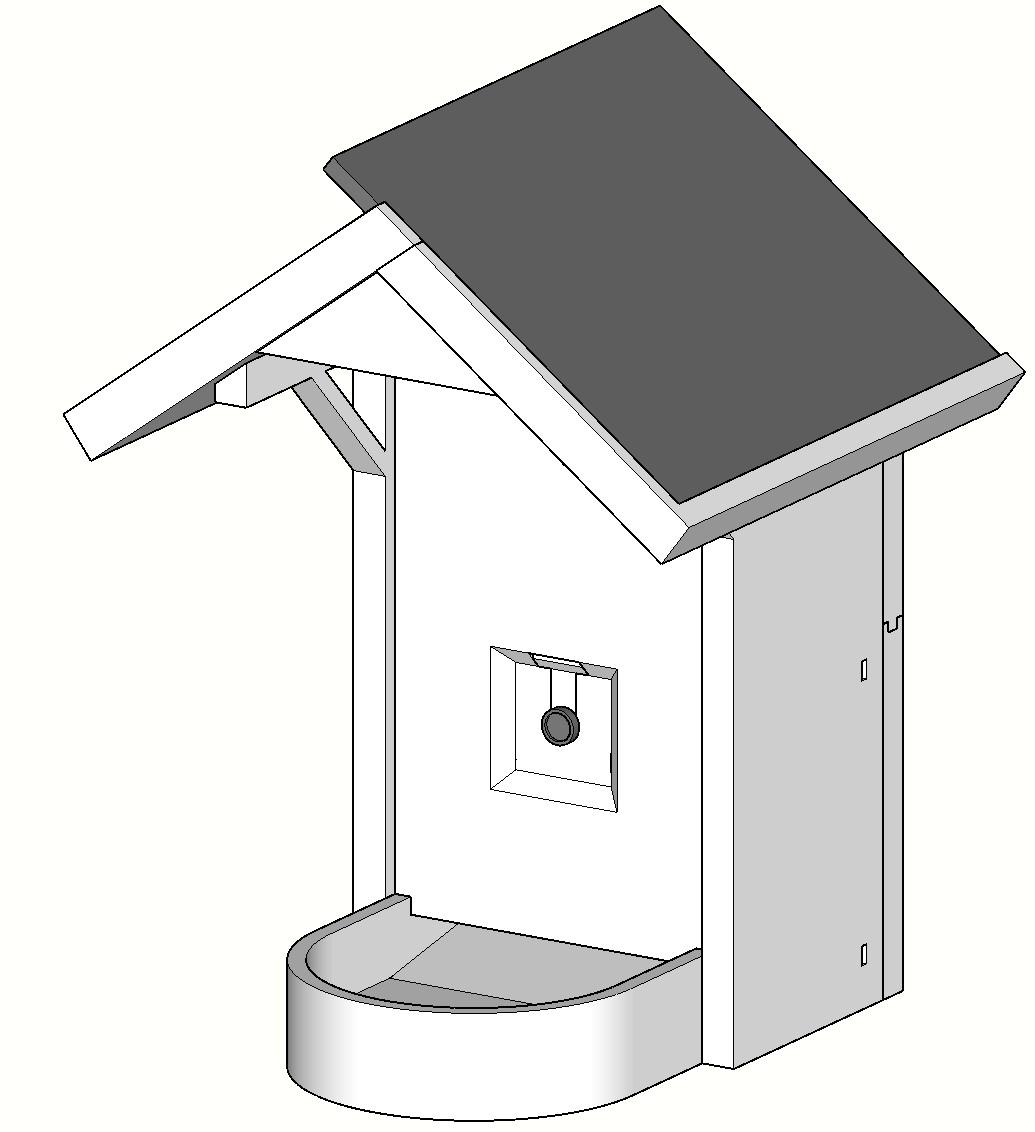
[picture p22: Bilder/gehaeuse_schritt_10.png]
    
</p>

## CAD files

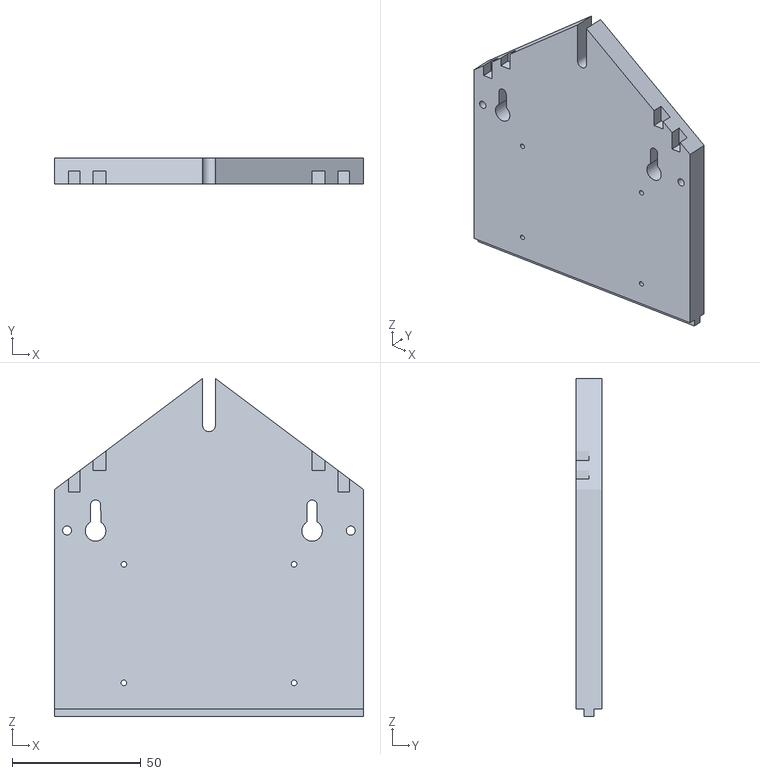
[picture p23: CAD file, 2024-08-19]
Gehäuse/Back_Wall_Top.stl
120.0 x 10.0 x 131.1

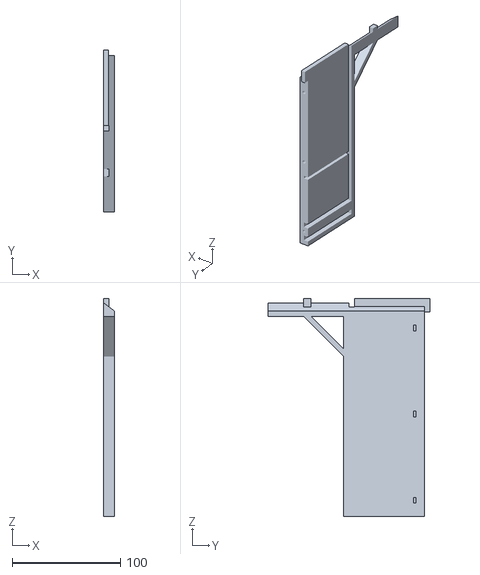
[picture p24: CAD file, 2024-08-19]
Gehäuse/Right_Wall.stl
10.0 x 150.0 x 201.5

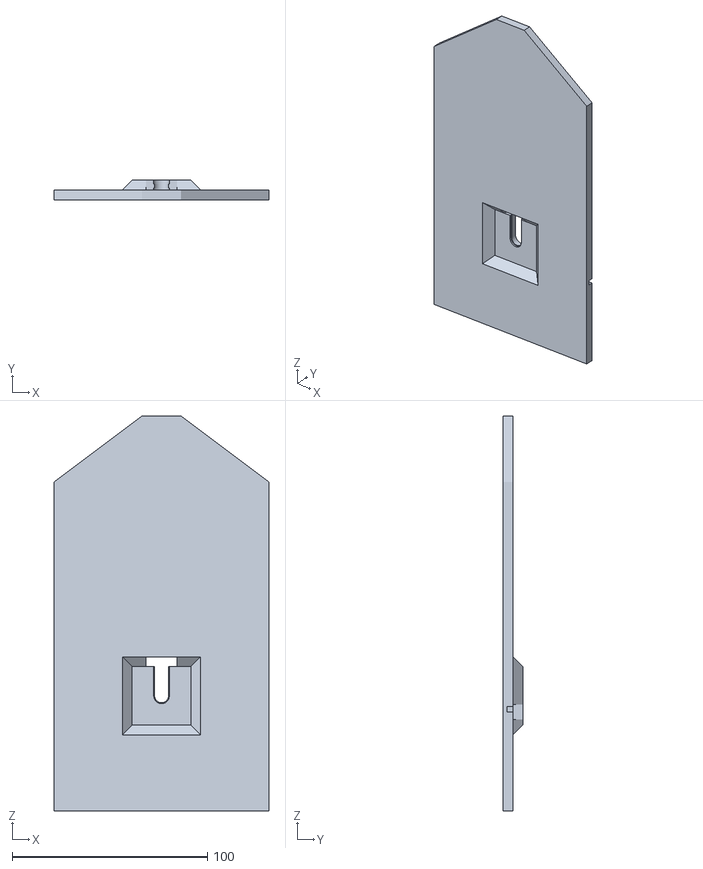
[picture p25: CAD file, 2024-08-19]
Gehäuse/Front_Wall.stl
110.0 x 10.0 x 202.5

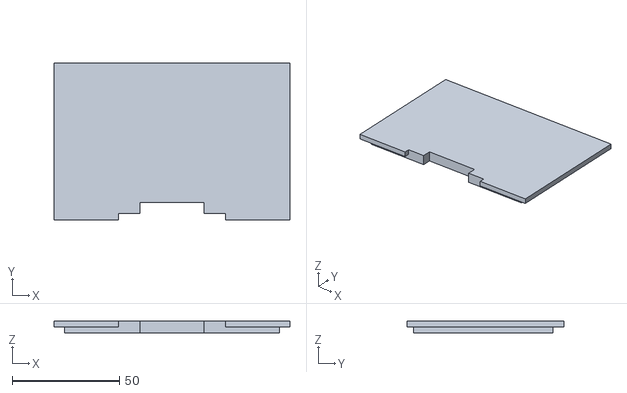
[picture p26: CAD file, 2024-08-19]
Gehäuse/Separator.stl
110.0 x 73.0 x 5.50

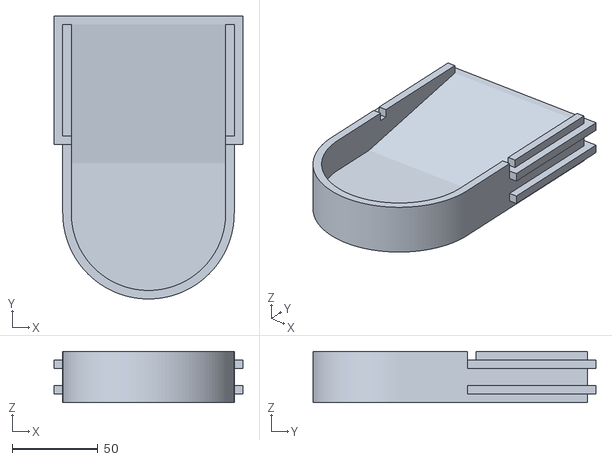
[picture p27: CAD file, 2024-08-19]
Gehäuse/Bottom_Tray.stl
110.0 x 165.0 x 30.0

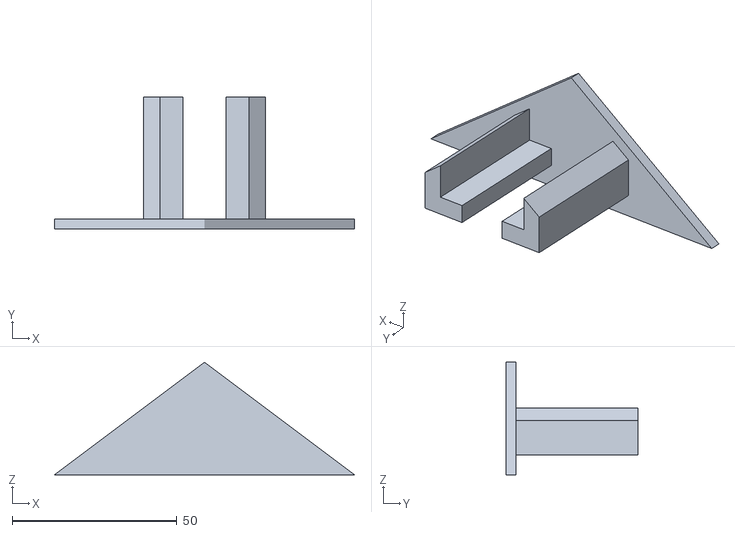
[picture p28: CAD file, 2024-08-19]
Gehäuse/PIR_Insert.stl
91.0 x 40.0 x 34.1

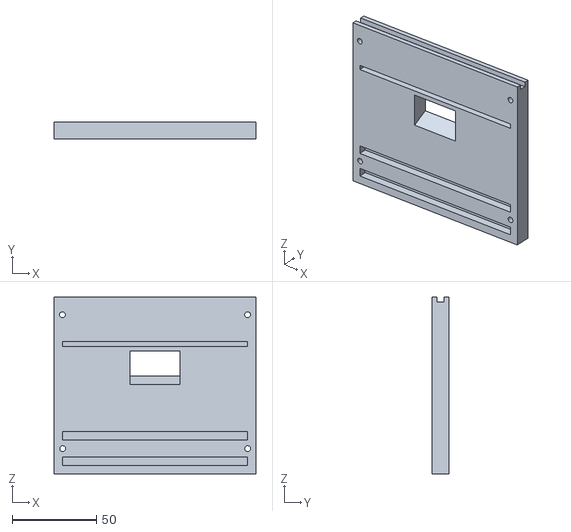
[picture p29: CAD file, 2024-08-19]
Gehäuse/Back_Wall_Bottom.stl
120.0 x 10.0 x 105.0

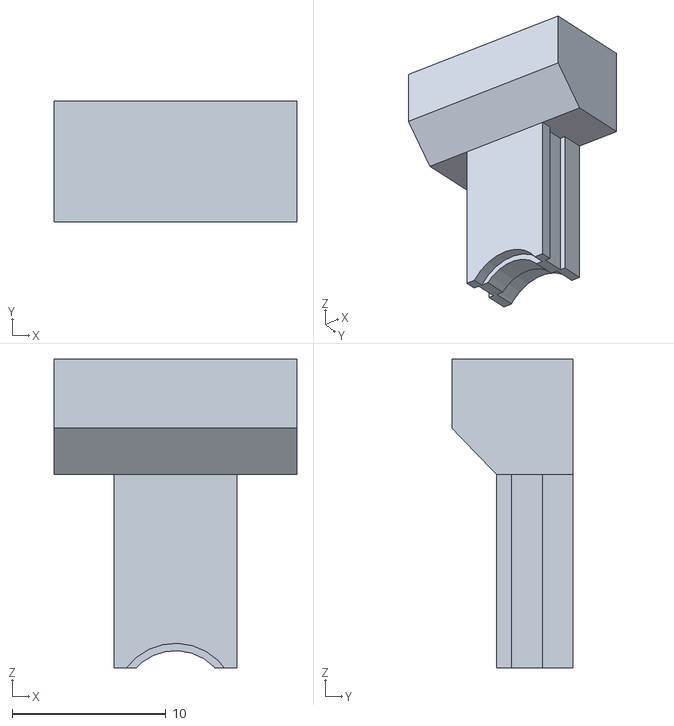
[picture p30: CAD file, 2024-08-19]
Gehäuse/Cam_Insert.stl
15.8 x 7.90 x 20.1

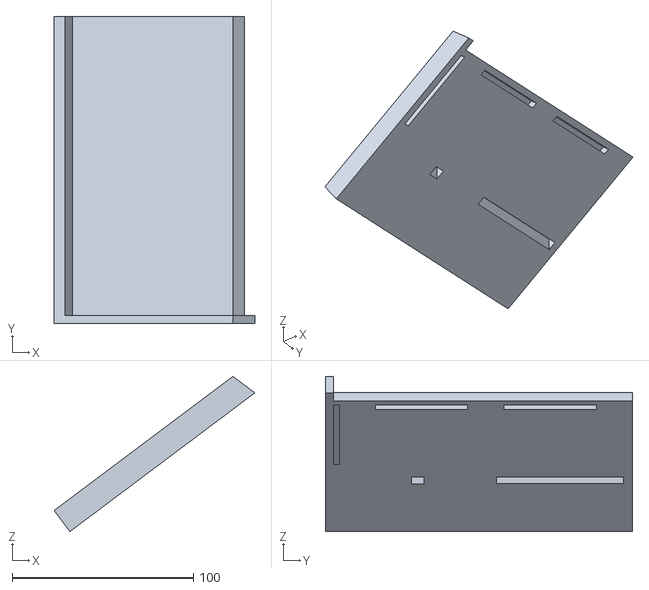
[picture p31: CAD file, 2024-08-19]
Gehäuse/Left_Roof.stl
110.8 x 169.5 x 85.6

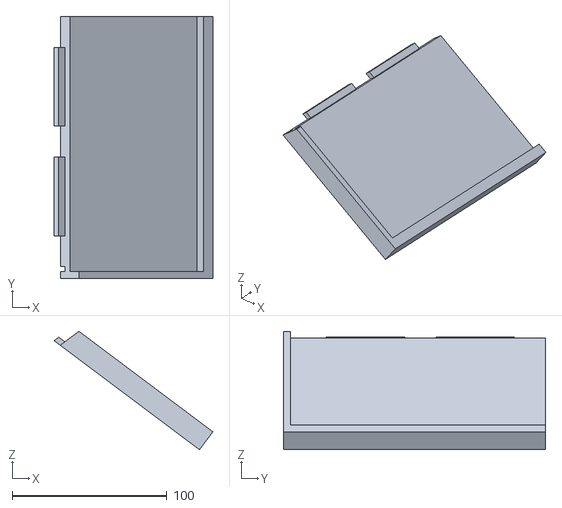
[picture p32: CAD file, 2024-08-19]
Gehäuse/Right_Roof.stl
102.7 x 169.5 x 76.6

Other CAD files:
Gehäuse/Left_Wall.stl
Gehäuse/Vogelfutterautomat.skp

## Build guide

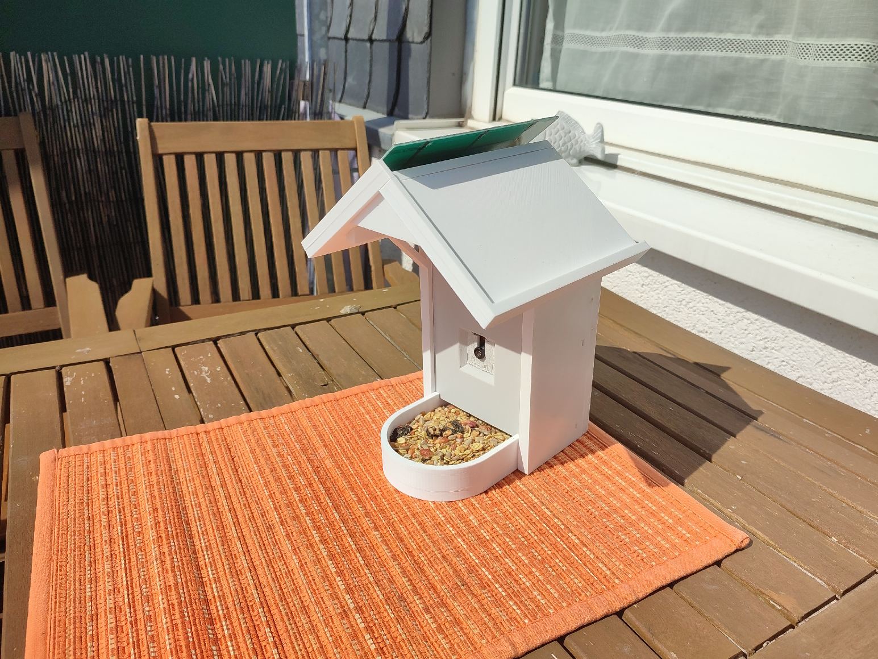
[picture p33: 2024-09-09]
Bilder/outdoortest-versuchsaufbau.jpg

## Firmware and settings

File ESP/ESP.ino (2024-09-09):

#include <Arduino.h>

/* Konfiguration */
//Für Debugging-Zwecke: aktiviert die UART-Schnittstelle
#define SERIAL_DEBUG

//Bestimmt, ob Daten zwischengespeichert werden oder direkt hochgeladen werden
//Mögliche Werte:
// DIREKT_UPLOAD - Aufnahmen werden direkt per WLAN an den Server übertragen
// TAEGLICHER_UPLOAD - Aufnahmen werden auf der SD-Karte zwischengespeichert und 1x täglich bei Auslösung des RTC-Alarms hochgeladen
// LOKAL - Aufnahmen werden nur auf der SD-Karte gespeichert
#define DATEN_MODUS DIREKT_UPLOAD

//Wie lange soll gewartet werden, bevor ein Foto aufgenommen wird. Wird für automatische Belichtungssteuerung verwendet.
#define WARTE_VOR_FOTO 2

//Bestimmen, wie lang, in Sekunden, die jeweiligen Audioaufnahmen ausfallen sollen. Maximalwert: 240 Sekunden
#define AUDIOAUFNAHME_KURZ_DAUER 5
#define AUDIOAUFNAHME_LANG_DAUER 60

//WLAN-Einstellungen
#define WIFI_SSID "****************"
#define WIFI_PASSWORD "****************"
#define UPLOAD_SERVER "xxx.xxx.xxx.xxx"
#define UPLOAD_PORT 80
#define UPLOAD_PATH "/upload.php"

/* Definitionen für die einzelnen Module */
/*    Kamera */
#include "esp_camera.h"
//Definition der Pin-Belegung für das OV2640 Kameramodul
#define CAMERA_MODEL_XIAO_ESP32S3
#define PWDN_GPIO_NUM     -1
#define RESET_GPIO_NUM    -1
#define XCLK_GPIO_NUM     10
#define SIOD_GPIO_NUM     40
#define SIOC_GPIO_NUM     39
#define Y9_GPIO_NUM       48
#define Y8_GPIO_NUM       11
#define Y7_GPIO_NUM       12
#define Y6_GPIO_NUM       14
#define Y5_GPIO_NUM       16
#define Y4_GPIO_NUM       18
#define Y3_GPIO_NUM       17
#define Y2_GPIO_NUM       15
#define VSYNC_GPIO_NUM    38
#define HREF_GPIO_NUM     47
#define PCLK_GPIO_NUM     13
#define LED_GPIO_NUM      21

bool cam_initialized = false;
bool cam_init();
bool take_and_upload_photo();
bool take_and_save_photo();
bool take_and_upload_photo_httpclient();

/*    SD-Karte */
#include "FS.h"
#include "SD.h"
bool storage_initialized = false;
bool storage_init();

/*    WLAN */
#include <WiFi.h>
#include <WiFiUdp.h>
#include <NTPClient.h>
bool wifi_initialized = false;
void wifi_init();
void wifi_deinit();
WiFiClient client;
#include <HTTPClient.h>

/*    RTC-Modul */
#include <Wire.h>
#include "RTClib.h"
bool rtc_initialized = false;
RTC_DS3231 rtc;
bool rtc_alarm_was_fired = false;
bool rtc_init();
bool rtc_set_time();
void rtc_print_config();

/*    Mikrofon */
#include <ESP_I2S.h>
#include "SPI.h"
I2SClass I2S;
#define SAMPLE_RATE 16000U
#define SAMPLE_BITS 16
#define WAV_HEADER_SIZE 44
#define VOLUME_GAIN 2
bool mic_init();
bool record_and_upload_wav(int duration_in_seconds);
bool record_and_save_wav(int duration_in_seconds);
void generate_wav_header(uint8_t *wav_header, uint32_t wav_size, uint32_t sample_rate);

/*    Arduino Kommunikation */
#define PIN_ARDUINO_SHUTDOWN_SIGNAL D0
void signal_shutdown();

/*    Debug-Ausgabe */
void log_debug(const char *msg) {
#ifdef SERIAL_DEBUG
  Serial.println(msg);
#endif
}

/* Hauptfunktion */
void setup() {
  pinMode(PIN_ARDUINO_SHUTDOWN_SIGNAL, OUTPUT);
  digitalWrite(PIN_ARDUINO_SHUTDOWN_SIGNAL, LOW);
  
#ifdef SERIAL_DEBUG
  Serial.begin(115200);
#endif
  //RTC initialisieren. Falls notwendig wird die aktuelle Zeit per WLAN/NTP gesetzt.
  //Es wird auch geprüft, ob der Alarm zurzeit ausgelöst ist.
  rtc_init();
  rtc_print_config();

  if(rtc_initialized && rtc_alarm_was_fired) {
    Serial.println("RTC wake");

    if(!mic_init()) {
      log_debug("ERR mic init failed");
    } else {
      #if DATEN_MODUS==DIREKT_UPLOAD
        record_and_upload_wav(AUDIOAUFNAHME_LANG_DAUER);
      #elif DATEN_MODUS==TAEGLICHER_UPLOAD || DATEN_MODUS==LOKAL
        record_and_save_wav(AUDIOAUFNAHME_LANG_DAUER);
      #endif

      #if DATEN_MODUS==TAEGLICHER_UPLOAD
        upload_all_files();
      #endif
    }
  } else {
    Serial.println("PIR wake");

    DateTime now = rtc.now();
    if(rtc_initialized && (now.hour() < 4 || now.hour() > 21)) { //TODO: Konfigurationsmöglichkeit
      log_debug("Keine Aufnahme in der Nacht.");
      signal_shutdown();
    }

    if(!cam_init()) {
      log_debug("ERR cam init failed");
    }else {
#if DATEN_MODUS==DIREKT_UPLOAD
      take_and_upload_photo();
#elif DATEN_MODUS==TAEGLICHER_UPLOAD || DATEN_MODUS==LOKAL
      take_and_save_photo();
#endif
    }

    if(!mic_init()) {
      log_debug("ERR mic init failed");
    } else {
#if DATEN_MODUS==DIREKT_UPLOAD
      record_and_upload_wav(AUDIOAUFNAHME_KURZ_DAUER);
#elif DATEN_MODUS==TAEGLICHER_UPLOAD || DATEN_MODUS==LOKAL
      record_and_save_wav(AUDIOAUFNAHME_KURZ_DAUER);
#endif
    }
  }
  Serial.println("DONE");
  wifi_deinit();
  signal_shutdown();
  while(1);
}

void loop() {
  if(rtc_initialized) {
    DateTime time = rtc.now();
    log_debug(time.timestamp(DateTime::TIMESTAMP_FULL).c_str());

    if(rtc.alarmFired(1)) {
      log_debug("RTC ALARM");
      delay(1000);
      rtc.clearAlarm(1);
    }
  } else {
    log_debug("INIT RTC FAILED");
  }
  
  delay(1000);
}

void signal_shutdown() {
  //Falls der RTC Alarm während der Laufzeit erneut ausgelöst wurde, zurücksetzen.
  //Zur Sicherheit, aber eigentlich nur für kurze Alarm-Abstände notwendig (Debug-Zwecke)
  if(rtc_initialized && rtc.alarmFired(1)) {
    rtc.clearAlarm(1);
  }

  digitalWrite(PIN_ARDUINO_SHUTDOWN_SIGNAL, HIGH);
  while(1) {
    if(rtc_initialized && rtc.alarmFired(1)) {
      rtc.clearAlarm(1);
    }
    delay(1000);
  }
}

//Initialisiert das Real-Time-Clock Modul und gibt zurück, ob dieser Vorgang erfolgreich war. Genauer bedeutet dies:
// 1. I2C Kommunikation wird hergestellt
// 2. Prüfe, ob Alarm ausgelöst wurde
// 3. Falls das RTC-Modul seinen Zustand verloren hat, neu konfigurieren
// 4. Alarm setzen
bool rtc_init() {
  log_debug("BEGIN rtc_init");
  if(rtc_initialized) {
    log_debug("rtc_init: already initialised");
    return true;
  }
  if(!rtc.begin()) {
    log_debug("rtc_init ERR rtc.begin()");
    return false;
  }
  
  rtc_alarm_was_fired = rtc.alarmFired(1);
  //Falls das RTC-Modul zurückgesetzt wurde wird es hier neu konfiguriert
  if(rtc.lostPower()) {
    log_debug("rtc_init: power was lost, initializing...");
    rtc.writeSqwPinMode(DS3231_OFF); //SQW-Pin kann als Signal-Generator verwendet werden, hier jedoch als Alarm-Pin
    rtc.disable32K(); //Signal-Generator-Pin wird nicht verwendet, deaktivieren
    log_debug("rtc_init: lost power, re-init");
    if(!rtc_set_time()) {
      return false;
    }
    rtc.disableAlarm(2);
  }
  
  //Alarme zurücksetzen
  rtc.clearAlarm(1);
  rtc.clearAlarm(2);

  //Alarm für 5 Uhr morgens stellen
  //DS3231_A1_Hour -> Alarm auslösen, wenn Stunde, Minute und Sekunde mit der gestellten Zeit übereinstimmen
  rtc.setAlarm1(DateTime(2000, 1, 1, 5, 0, 0), DS3231_A1_Hour);

  rtc_initialized = true;
  log_debug("rtc_init DONE");
  return true;
}

bool rtc_set_time() {
  log_debug("BEGIN rtc_set_time");
  wifi_init(); //TODO: disable wifi at end of function
  WiFiUDP udp;
  NTPClient ntp(udp);
  //2 Stunden verschiebung zwischen UTC (Unix Time) und Berlin TZ
  ntp.setTimeOffset(2 * 60 * 60);
  ntp.begin();
  
  if(!ntp.update()) {
    log_debug("rtc_set_time ERR ntp.update()");
    return false;
  }
  
  log_debug("rtc_set_time: setting time");
  rtc.adjust(DateTime(ntp.getEpochTime()));

  ntp.end();
  return true;
}

//Gibt die aktuelle Uhrzeit und den Zustand von Alarm1 aus.
void rtc_print_config() {
  #ifndef SERIAL_DEBUG
  return;
  #endif
  if(!rtc_initialized) {
    Serial.println("rtc_print_config ERR not initialized");
    return;
  }
  Serial.println("Time       = " + rtc.now().timestamp(DateTime::timestampOpt::TIMESTAMP_FULL));
  DateTime alarm = rtc.getAlarm1();
  Serial.println("Alarm 1 Time = " + alarm.timestamp(DateTime::timestampOpt::TIMESTAMP_FULL));

  Ds3231Alarm1Mode alarm_mode = rtc.getAlarm1Mode();
  Serial.print("Alarm 1 Mode = ");
  switch (alarm_mode) {
  case DS3231_A1_PerSecond:
    Serial.println("DS3231_A1_PerSecond");
    break;
  case DS3231_A1_Second:
    Serial.println("DS3231_A1_Second");
    break;
  case DS3231_A1_Minute:
    Serial.println("DS3231_A1_Minute");
    break;
  case DS3231_A1_Hour:
    Serial.println("DS3231_A1_Hour");
    break;
  case DS3231_A1_Date:
    Serial.println("DS3231_A1_Date");
    break;
  case DS3231_A1_Day:
    Serial.println("DS3231_A1_Day");
    break;
  default:
    Serial.println("ERR");
  }
}

//Erstellt einen String anhand der aktuellen Uhrzeit im Format "YYYY-MM-DD_hh-mm-ss". Wird für Vergebung von Dateinamen verwendet.
String rtc_get_filename() {
  if(!rtc_initialized) {
    Serial.println("rtc_get_filename ERR not initialized");
    return String("default");
  }
  String fn = rtc.now().timestamp(DateTime::timestampOpt::TIMESTAMP_FULL);
  fn.replace(":", "-");
  return fn;
}

//Initialisiert die Kamera und gibt zurück, ob der Vorgang erfolgreich war.
//Hier wird die Pin-Belegung des Moduls, die Bildqualität sowie weitere Sensor-Einstellungen (z.B. Spiegelung) gesetzt.
bool cam_init() {
  log_debug("Initialising camera...");
  static camera_config_t config = {
      .pin_pwdn       = PWDN_GPIO_NUM,
      .pin_reset      = RESET_GPIO_NUM,
      .pin_xclk       = XCLK_GPIO_NUM,
      .pin_sccb_sda   = SIOD_GPIO_NUM,
      .pin_sccb_scl   = SIOC_GPIO_NUM,
      .pin_d7         = Y9_GPIO_NUM,
      .pin_d6         = Y8_GPIO_NUM,
      .pin_d5         = Y7_GPIO_NUM,
      .pin_d4         = Y6_GPIO_NUM,
      .pin_d3         = Y5_GPIO_NUM,
      .pin_d2         = Y4_GPIO_NUM,
      .pin_d1         = Y3_GPIO_NUM,
      .pin_d0         = Y2_GPIO_NUM,
      .pin_vsync      = VSYNC_GPIO_NUM,
      .pin_href       = HREF_GPIO_NUM,
      .pin_pclk       = PCLK_GPIO_NUM,

      .xclk_freq_hz   = 20000000,
      .pixel_format   = PIXFORMAT_JPEG,
      .frame_size     = FRAMESIZE_UXGA, //Die Auflösung des Fotos: FRAMESIZE_ + QVGA|CIF|VGA|SVGA|XGA|SXGA|UXGA
      .jpeg_quality   = 12, //JPEG-Qualität: zwischen 0 und 63 (niedriger = bessere Qualität)
      .fb_count       = 1,
      .fb_location    = CAMERA_FB_IN_PSRAM, //Bestimmt, dass die Frame-Buffer im PSRAM angelegt werden.
      .grab_mode      = CAMERA_GRAB_WHEN_EMPTY
  };
  
  esp_err_t err = esp_camera_init(&config);
  if (err != ESP_OK) {
    Serial.printf("\tFAILED Camera init failed");
    return false;
  }

  sensor_t *s = esp_camera_sensor_get();
  s->set_brightness(s, -1);     // -2 to 2
  s->set_contrast(s, 0);       // -2 to 2
  s->set_saturation(s, 0);     // -2 to 2
  s->set_special_effect(s, 0); // 0 to 6 (0 - No Effect, 1 - Negative, 2 - Grayscale, 3 - Red Tint, 4 - Green Tint, 5 - Blue Tint, 6 - Sepia)
  s->set_whitebal(s, 1);       // 0 = disable , 1 = enable
  s->set_awb_gain(s, 1);       // 0 = disable , 1 = enable
  s->set_wb_mode(s, 1);        // 0 to 4 - if awb_gain enabled (0 - Auto, 1 - Sunny, 2 - Cloudy, 3 - Office, 4 - Home)
  s->set_exposure_ctrl(s, 1);//  // 0 = disable , 1 = enable
  s->set_aec2(s, 1);           // 0 = disable , 1 = enable
  s->set_ae_level(s, 0);       // -2 to 2
  s->set_aec_value(s, 250);    // 0 to 1200
  s->set_gain_ctrl(s, 1);      // 0 = disable , 1 = enable
  s->set_agc_gain(s, 0);       // 0 to 30
  s->set_gainceiling(s, (gainceiling_t)0);  // 0 to 6
  s->set_bpc(s, 0);            // 0 = disable , 1 = enable
  s->set_wpc(s, 1);            // 0 = disable , 1 = enable
  s->set_raw_gma(s, 1);        // 0 = disable , 1 = enable
  s->set_lenc(s, 1);           // 0 = disable , 1 = enable
  s->set_hmirror(s, 1);        // 0 = disable , 1 = enable
  s->set_vflip(s, 1);          // 0 = disable , 1 = enable
  s->set_dcw(s, 1);            // 0 = disable , 1 = enable
  s->set_colorbar(s, 0);       // 0 = disable , 1 = enable

  Serial.println("\tFinished.");
  return true;
}

//Stellt die Verbindung zum WLAN her und gibt zurück, ob die Verbindung erfolgreich war.
//TODO: Momentan gibt es hier keine Maximalzeit; es wird unendlich lang probiert.
void wifi_init() {
  if(wifi_initialized) return;
  Serial.print("Initialisiere WLAN...");
  WiFi.mode(WIFI_STA);
  WiFi.begin(WIFI_SSID, WIFI_PASSWORD);
  WiFi.setSleep(false);
  while (WiFi.status() != WL_CONNECTED) {
    delay(500);
    Serial.print(".");
  }

  Serial.println();
  Serial.println("\tWLAN-Verbindung hergestellt");
  wifi_initialized = true;
}

//Trennt die WLAN-Verbindung.
void wifi_deinit() {
  if(!wifi_initialized) return;
  Serial.println("Deaktiviere WLAN...");
  WiFi.disconnect(); 
  WiFi.mode(WIFI_OFF);
  Serial.println("\tWLAN-Verbindung getrennt");
  wifi_initialized = false;
}

bool storage_init() {
  if(storage_initialized) return true;
  Serial.println("Initialisiere SD-Karte...");
  if(!SD.begin(21)) {
    Serial.println("\tFEHLER SD.begin() ist fehlgeschlagen");
    return false;
  }
  
  Serial.println("\tSD-Karte initialisiert");
  storage_initialized = true;
  return true;
}

//Nimmt ein Foto auf und startet sofort den Upload an den Server.
bool take_and_upload_photo() {
  Serial.println("Foto aufnehmen und hochladen...");
  delay(WARTE_VOR_FOTO * 1000);
  Serial.println("\tFrame-Buffer holen...");
  camera_fb_t * fb = esp_camera_fb_get();
  if(!fb) {
    Serial.println("\tFEHLER Frame-Buffer konnte nicht akquiriert werden");
    return false;;
  }
  
  if(!wifi_initialized) {
    wifi_init();
  }
  
  Serial.print("\tIP-Addresse: ");
  Serial.println(WiFi.localIP());
  Serial.print("\tVerbindung zum Server ");
  Serial.print(UPLOAD_SERVER);
  Serial.println("...");

  unsigned long transmission_start_time = millis();
  if(!client.connect(UPLOAD_SERVER, UPLOAD_PORT)) {
    Serial.println("\tFEHLER Server-Verbindung fehlgeschlagen");
    return false;
  }

  Serial.println("\tVerbunden");
  String fn = rtc_get_filename();
  Serial.println("\tDateiname: " + fn);
  String head = "--File\r\nContent-Disposition: form-data; name=\"uploadFile\"; filename=\"" + fn + ".jpg\"\r\nContent-Type: image/jpeg\r\n\r\n";
  String tail = "\r\n--File--\r\n";

  uint32_t totalLen = fb->len + head.length() + tail.length();

  Serial.println("\tBeginne Upload...");
  Serial.println("\t\tHeaders");
  client.println("POST /esp32/upload.php HTTP/1.1");
  client.println("Host: " + String(UPLOAD_SERVER));
  client.println("Content-Length: " + String(totalLen));
  client.println("Content-Type: multipart/form-data; boundary=File");
  client.println();
  client.print(head);

  uint8_t *fbBuf = fb->buf;
  size_t fbLen = fb->len;
  size_t packetSize = 4096;
  Serial.print("\t\tBilddaten (");
  Serial.print(fbLen);
  Serial.println("b)");
  Serial.println("Fortschritt:");
  for(size_t n = 0; n < fbLen; n += packetSize) Serial.print(".");
  Serial.println();

  for (size_t n = 0; n<fbLen; n = n + packetSize) {
    if (n + packetSize < fbLen) {
      client.write(fbBuf, packetSize);
      fbBuf += packetSize;
    }
    else if (fbLen % packetSize > 0) {
      size_t remainder = fbLen % packetSize;
      client.write(fbBuf, remainder);
    }
    Serial.print(".");
  }
  Serial.println();
  Serial.println("\t\tFrame-Buffer freigeben und Kamera deaktivieren");
  esp_camera_fb_return(fb);
  esp_camera_deinit();
  Serial.println("\t\tFooter");
  client.print(tail);
  
  Serial.print("\tUpload abgeschlossen. Dauer: ");
  Serial.print(millis() - transmission_start_time);
  Serial.println(" ms");
  Serial.println("\tWarte auf Antwort des Servers...");

  int timeoutTimer = 10000;
  long startTimer = millis();
  String status = "";
  boolean done = false;
  while (!done && (startTimer + timeoutTimer) > millis()) {
    delay(10);
    //Es wird nur die erste Zeile ausgelesen, um den HTTP Response Code zu prüfen
    while (client.available()) {
      char c = client.read();
      Serial.print(c);
      if (c == '\r' || c == '\n') {
        if (status.length() > 0) {
          done = true;
          break;
        }
      }
      else {
        status += String(c);
      }
    }
  }
  Serial.println();
  Serial.println("\tBeende Server-Verbindung");
  client.stop();
  
  Serial.print("\tStatus: ");
  Serial.println(String(status).c_str());
  if(status.indexOf("200") > -1) {
    return true;
  } else {
    return false;
  }
}

//Nimmt ein Foto auf und speichert dieses auf der SD-Karte.
bool take_and_save_photo() {
  Serial.println("Foto aufnehmen und auf SD-Karte speichern...");
  Serial.println("\tEin paar Sekunden warten...");
  delay(WARTE_VOR_FOTO * 1000);
  Serial.println("\tFrame-Buffer holen...");
  camera_fb_t * fb = esp_camera_fb_get();

  if(!fb) {
    Serial.println("\tFEHLER Frame-Buffer konnte nicht akquiriert werden");
    return false;
  }
  
  Serial.println("\tInitialisiere SD-Karte...");
  if(!SD.begin(21)){
      log_debug("\tFEHLER SD-Karte konnte nicht initialisiert werden");
      return false;
  }

  uint8_t cardType = SD.cardType();
  if(cardType == CARD_NONE){
      log_debug("\tFEHLER Keine SD-Karte eingesteckt");
      return false;
  }

  //Das Foto erhält einen Dateinamen anhand der aktuellen Uhrzeit
  String timestamp = rtc_get_filename();
  String fileName = "/" + timestamp + ".jpg";
  Serial.println("\tFoto wird gespeichert unter: " + fileName);
  File file = SD.open(fileName.c_str(), FILE_WRITE);
  if(!file) {
    Serial.println("\tFEHLER Foto konnte nicht gespeichert werden");
    return false;
  }
  file.write(fb->buf, fb->len);
  file.close();
  
  Serial.println("\t\tFrame-Buffer freigeben und Kamera deaktivieren");
  esp_camera_fb_return(fb);
  esp_camera_deinit();
  return true;
}

bool mic_init() {
  Serial.println("Initialisiere Mikrofon...");
  Serial.println("\tBeginne I2S-Kommunikation");
  I2S.setPinsPdmRx(42, 41);

  if (!I2S.begin(I2S_MODE_PDM_RX, 16000, I2S_DATA_BIT_WIDTH_16BIT, I2S_SLOT_MODE_MONO)) {
    Serial.println("\tFEHLER I2S-Kommunikation fehlgeschlagen");
    return false;
  }

  Serial.println("\tInitialisierung abgeschlossen");
  return true;
}

/*
  Führt eine Audioaufnahme durch und läd diese direkt als WAV-Datei hoch (ohne Verwendung der SD-Karte)
  Ablauf:
  - 1. Header generieren
  - 2. Audioaufnahme durchführen (Dauer wird bestimmt durch RECORD_TIME)
  - 3. Samples skalieren um Lautstärke zu erhöhen (bestimmt durch VOLUME_GAIN)
  - 4. WLAN aktivieren
  - 5. Verbindung zum Zielserver herstellen (UPLOAD_SERVER / UPLOAD_PORT)
  - 6. HTTP POST durchführen, um WAV-Datei hochzuladen
  - 7. Auf Antwort des Servers warten, um festzustellen, ob das Hochladen erfolgreich war
  - 8. WLAN deaktivieren
*/
bool record_and_upload_wav(int duration_in_seconds) {
  Serial.println("Audio aufnehmen und hochladen...");
  Serial.println("\tGeneriere WAV-Header");
  uint32_t record_size = (SAMPLE_RATE * SAMPLE_BITS / 8) * duration_in_seconds;
  uint32_t sample_size = 0;
  uint8_t wav_header[WAV_HEADER_SIZE];
  generate_wav_header(wav_header, record_size, SAMPLE_RATE);

  Serial.println("\tLege Buffer für Samples an");
  uint8_t *rec_buffer = (uint8_t *)ps_malloc(record_size);
  if (rec_buffer == NULL) {
    Serial.println("\tFEHLER malloc ist fehlgeschlagen");
    return false;
  }

  Serial.println("\tStarte Aufnahme...");
  sample_size = I2S.readBytes((char *)rec_buffer, record_size);
  if (sample_size == 0) {
    Serial.println("\tFEHLER Aufnahme fehlgeschlagen");
    return false;
  } else {
    Serial.printf("\t%d bytes aufgenommen\n", sample_size);
  }
  
  Serial.println("\tErhöhe Lautstärke der Aufnahme");
  for (uint32_t i = 0; i < sample_size; i += SAMPLE_BITS/8) {
    (*(uint16_t *)(rec_buffer+i)) <<= VOLUME_GAIN;
  }

  if(!wifi_initialized) {
    wifi_init();
    if(!wifi_initialized)
      return false;
  }
  Serial.println("\tVerbindung zum Server wird hergestellt...");
  if(!client.connect(UPLOAD_SERVER, UPLOAD_PORT)) {
    Serial.println("\tFEHLER Server-Verbindung fehlgeschlagen");
    return false;
  }
  Serial.println("\tVerbindung zum Server erfolgreich");
  String fn = rtc_get_filename();
  Serial.println("\tDateiname: " + fn);

  Serial.println("\tBeginne Upload...");
  String head = "--File\r\nContent-Disposition: form-data; name=\"uploadFile\"; filename=\"" + fn + ".wav\"\r\nContent-Type: audio/wav\r\n\r\n";
  String tail = "\r\n--File--\r\n";

  uint32_t totalLen = head.length() + WAV_HEADER_SIZE + record_size + tail.length();
  log_debug("\t\tHeader");
  client.println("POST " + String(UPLOAD_PATH) + " HTTP/1.1");
  client.println("Host: " + String(UPLOAD_SERVER));
  client.println("Content-Length: " + String(totalLen));
  client.println("Content-Type: multipart/form-data; boundary=File");
  client.println();

  Serial.println("\t\tForm-Header");
  client.print(head);
  Serial.println("\t\tWAV-Header");
  client.write(wav_header, WAV_HEADER_SIZE);
  Serial.println("\t\tWAV-Daten");
  client.write(rec_buffer, record_size);
  Serial.println("\t\tForm-Footer");
  client.print(tail);
  Serial.println("\t\tUpload abgeschlossen");
  Serial.println("\tBuffer wird freigegeben");
  free(rec_buffer);

  Serial.println("\tWarte auf Antwort des Servers");
  String status = "";
  boolean done = false;
  //Auf Antwort des Servers warten
  while (!done) {
    delay(10);
    //Es wird nur die erste Zeile ausgelesen, um den HTTP Response Code zu prüfen
    while (client.available()) {
      char c = client.read();
      if (c == '\r' || c == '\n') {
        if (status.length() > 0) {
          done = true;
          break;
        }
      }
      else {
        status += String(c);
      }
    }
  }
  client.stop();
  
  Serial.print("\tAntwort: ");
  Serial.println(status);
  if(status.indexOf("200") > -1) {
    return true;
  } else {
    return false;
  }
}
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

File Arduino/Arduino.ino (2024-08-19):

//Für Debugging-Zwecke: aktiviert die UART-Schnittstelle
#define ENABLE_SERIAL

#include "LowPower.h"

#define RTC_WAKE_PIN 2
#define PIR_WAKE_PIN 3
#define ESP_POWER_PIN A0
#define ESP_SIGNAL_PIN 10

void isr_rtc_wake();
void isr_pir_wake();

char wakeup_reason = 0;

void setup() {
#ifdef ENABLE_SERIAL
  Serial.begin(115200);
#endif

  pinMode(RTC_WAKE_PIN, INPUT_PULLUP);
  pinMode(PIR_WAKE_PIN, INPUT);
  pinMode(ESP_POWER_PIN, OUTPUT);
  digitalWrite(ESP_POWER_PIN, LOW);
  pinMode(ESP_SIGNAL_PIN, INPUT);
}

void loop() {
#ifdef ENABLE_SERIAL
  Serial.println("Betrete Schlafmodus");
  Serial.flush();
  delay(200);
#endif

  attachInterrupt(digitalPinToInterrupt(RTC_WAKE_PIN), isr_rtc_wake, LOW);
  attachInterrupt(digitalPinToInterrupt(PIR_WAKE_PIN), isr_pir_wake, HIGH);
  LowPower.powerDown(SLEEP_FOREVER, ADC_OFF, BOD_OFF);
  detachInterrupt(digitalPinToInterrupt(RTC_WAKE_PIN));
  detachInterrupt(digitalPinToInterrupt(PIR_WAKE_PIN));

  Serial.print(millis());
  Serial.println(" - Aufgeweckt");
  unsigned long timeout = 0;
  switch(wakeup_reason) {
    case 1:
      Serial.println("Aufweckgrund: RTC");
      //RTC wakeup -> 1 Minute Audio-Aufnahme
      timeout = 80 * 1000;
      break;
    case 2:
      Serial.println("Aufweckgrund: PIR");
      //PIR wakeup -> Foto + 5 Sekunden Audio-Aufnahme
      timeout = 45 * 1000;
    break;
    default:
      Serial.println("Aufweckgrund: Unbekannt!");
      break;
  }
  wakeup_reason = 0;

  //ESP hochfahren
  Serial.println("ESP wird hochgefahren");
  digitalWrite(ESP_POWER_PIN, HIGH);
  delay(1000);
  
  Serial.println("Warte auf Signal vom ESP...");
  unsigned long startTime = millis();
  Serial.println(startTime);
  //TODO: timeout
  while(digitalRead(ESP_SIGNAL_PIN) != HIGH) {
    /*if (millis() > (startTime + timeout)) {
      Serial.println("timeout");
      break;
    }
    delay(50);*/
  }
  
  Serial.println("ESP wird heruntergefahren");
  digitalWrite(ESP_POWER_PIN, LOW);
}

void isr_rtc_wake() { 
  wakeup_reason = 1;
}

void isr_pir_wake() {
  wakeup_reason = 2;
}

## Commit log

2024-08-19 3D-Druck-Dateien hinzugefügt
    [Back_Wall_Bottom.stl, Back_Wall_Top.stl, Bottom_Tray.stl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]
2024-08-19 README.md aktualisiert und Server-Software hinzugefügt
2024-08-19 README.md aktualisiert und ESP.ino angepasst
2024-09-09 README.md aktualisiert
    * Platinen-Dateien hinzugefügt
    [Platine.fzz]
2024-09-09 README.md aktualisiert: Gehäuse
    [Vogelfutterautomat.skp]
2024-09-09 README.md aktualisiert: Zusammenbau des Gehäuses
